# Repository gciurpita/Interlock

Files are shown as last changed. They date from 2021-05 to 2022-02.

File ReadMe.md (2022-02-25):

### RR Interlock - Bill Lupoli's New Haven



Arduino interlock route controller,
aligns multiple turnouts through interlock
by pressing buttons at either end of route.

Controller uses hardware shown at right.
~12V input top left to ~6V down converter to Arduino UNO board bottom left.
Three custom Tortoise Driver and I/O PCBs
using MCP23017 I2C I/O expander
to control up to 8 tortoise switch machines using LM324 op-amps and
eight GPIOs.

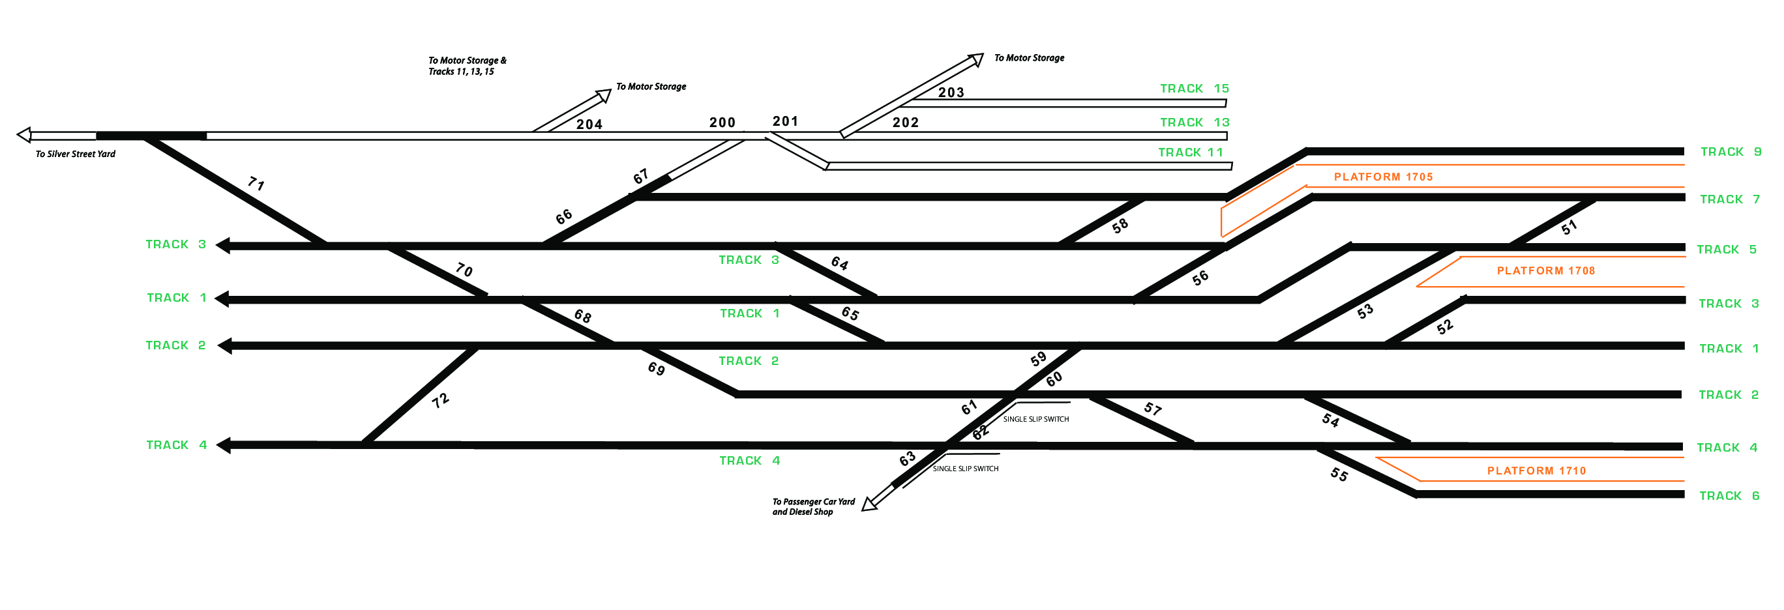
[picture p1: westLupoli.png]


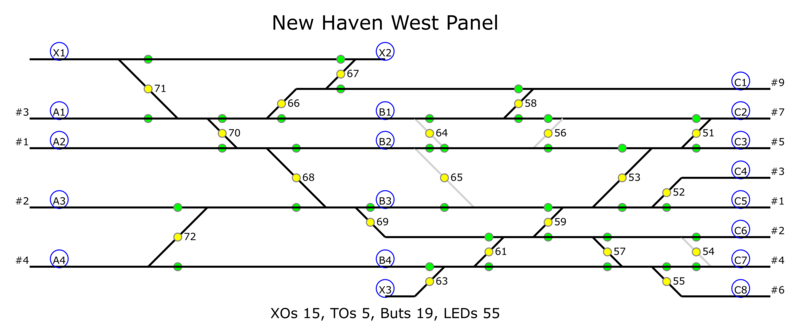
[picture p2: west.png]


<!-- -----------------------------------------------  ---------------------- -->
<h4> PCB Wire Connections </h4>

<table border=1 cellspacing=0 align=right>
 <tr> <th colspan=2> PCB 4
 <tr> <th> Sw <th> But
 <tr> <td align=center> &nbsp; <td align=center>  &nbsp;
 <tr> <td align=center> &nbsp; <td align=center>  &nbsp;
 <tr> <td align=center> &nbsp; <td align=center>  &nbsp;
 <tr> <td align=center> &nbsp; <td align=center>  &nbsp;

 <tr> <td align=center> &nbsp; <td align=center>  &nbsp;
 <tr> <td align=center> &nbsp; <td align=center>  &nbsp;
 <tr> <td align=center> &nbsp; <td align=center>  &nbsp;
 <tr> <td align=center> &nbsp; <td align=center>  &nbsp;
</table>

<table border=1 cellspacing=0 align=right>
 <tr> <th colspan=2> PCB 3
 <tr> <th> Sw <th> But
 <tr> <td align=center>  69 <td align=center>  A1
 <tr> <td align=center>  70 <td align=center>  A2
 <tr> <td align=center>  71 <td align=center>  A3
 <tr> <td align=center>  72 <td align=center>  A4
 <tr> <td align=center> &nbsp; <td align=center> B1
 <tr> <td align=center> &nbsp; <td align=center> B2
 <tr> <td align=center> &nbsp; <td align=center> B3
 <tr> <td align=center> &nbsp; <td align=center> B4
</table>

<table border=1 cellspacing=0 align=right>
 <tr> <th colspan=2> PCB 2
 <tr> <th> Sw <th> But
 <tr> <td align=center>  59 <td align=center>  C1
 <tr> <td align=center>  61 <td align=center>  C2
 <tr> <td align=center>  63 <td align=center>  C3
 <tr> <td align=center>  64 <td align=center>  C4
 <tr> <td align=center>  65 <td align=center>  C5
 <tr> <td align=center>  66 <td align=center>  C6
 <tr> <td align=center>  67 <td align=center>  C7
 <tr> <td align=center>  68 <td align=center>  C8
</table>

<table border=1 cellspacing=0 align=right>
 <tr> <th colspan=2> PCB 1
 <tr> <th> Sw <th> But
 <tr> <td align=center>  51 <td align=center>  X1
 <tr> <td align=center>  52 <td align=center>  X2
 <tr> <td align=center>  53 <td align=center>  X3
 <tr> <td align=center>  54 <td align=center>  &nbsp;

 <tr> <td align=center>  55 <td align=center>  &nbsp;
 <tr> <td align=center>  56 <td align=center>  &nbsp;
 <tr> <td align=center>  57 <td align=center>  &nbsp;
 <tr> <td align=center>  58 <td align=center>  &nbsp;
</table>

<a href=https://i.imgur.com/RJTQaR7.jpg target="_blank">
</a>

<!-- -----------------------------------------------  ---------------------- -->
<h4> Panel Description  </h4>

<i>westIntLck.cpp</i> contains tables describing the panel:
buttons, turnouts and routes.
This description requires a minimal understanding of programming
to make modifications.

<p>
Descriptions of both buttons and turnouts
includes identifying the corresponding
chip and port bit along with a label.

<p>
Buttons are described in <i>butIos []</i>.
<i>Ba1</i> is a numeric symbol uniquely identifying each button,
the <i>B</i> prefix identifies it as a button and
<i>a1</i> corresponds to the label on the panel.
The <i>0, 0, "A1"</i> identifies the input on
chip 0, port bit 0 (the first or least significant bit) and
a text string label, <i>A1</i>.
There are at most 8 bits on each chip,
some spare bits are available.

<blockquote><pre>
const PROGMEM ButIo_t butIos [] = {
    { Ba1, { 0, 0, "A1" }},
    ...
    { Bc6, { 1, 5, "C6" }},
    ...
    { Bc9, { 2, 0, "C9" }},
    { Bx1, { 2, 1, "X1" }},
    { Bx2, { 2, 2, "X2" }},
    ...
    { B_0, { 0, 0, ""   }},
};
</blockquote></pre>

There is an entry for each switch machine position.
<i>s02r</i> is the variable name of the entry used in the <i>routes</i> table.
The first three fields, <i>2, R, 1</i>,
include a numeric value for the switch machine,
a symbol, <i>N/R</i> identifying the position as normal/reverse and
the bit value, 0/1 for that position.
The last three fields,
<i>0, 1, "s02r"</i>, like the button entry
specify the chip, port bit and label.

<blockquote><pre>
// machine address and polarity
const PROGMEM SwMach_t s02n = {  2, N, 0, { 0, 1, "s02n" }};
const PROGMEM SwMach_t s02r = {  2, R, 1, { 0, 1, "s02r" }};

const PROGMEM SwMach_t s14n = { 14, N, 0, { 1, 5, "s14n" }};
const PROGMEM SwMach_t s14r = { 14, R, 1, { 1, 5, "s14r" }};

const PROGMEM SwMach_t s21n = { 21, N, 0, { 2, 4, "s21n" }};
const PROGMEM SwMach_t s21r = { 21, R, 1, { 2, 4, "s21r" }};
</blockquote></pre>

Routes are described in the routes table, <i>routes []</i>.
Each entry specifies a pair a buttons and
one or more switch machine position references (i.e. pointers).

<blockquote><pre>
const PROGMEM Route_t routes [] = {
    { Ba1, Bc1, { &s21r, &s19n, &s15r, &s14n, &s06n }},
    { Ba1, Bc2, { &s21r, &s19n, &s15n, &s10n, &s06n }},
    ...
    { Ba4, Bc4, { &s20n, &s16n, &s17n, &s11n, &s12n, &s07n, &s02r, &s01n }},
    ...
}
</blockquote></pre>

Some routes are ambiguous,
a pair of buttons can select more than one route.
<blockquote><pre>
    { Ba4, Bc3, { &s20n, &s16n, &s17n, &s11n, &s12n, &s07n, &s02r, &s01r }},
    { Ba4, Bc3, { &s20r, &s16n, &s17n, &s11n, &s12n, &s07n, &s02r, &s01r }},
</blockquote>

The code repeatedly
* monitors the button input ports
* detects that two or more buttons have been pressed
* uses <i>butIos []</i> to match the chip and port bit to button IDs
* searches the routes table for an entry with that pair of buttons, and
* sets the corresponding bits to position the switch
for each machine in the route.

<!-- -----------------------------------------------  ---------------------- -->
<hr>
<h4> Code Description </h4>

<b>setup ()</b> 
sets the serial monitor bit rate,
configures pins 5-13 as outputs,
initializes the I2C interface (i.e. <i>Wire</i>) and
calls <i>i2cCfg ()</i> to configure the
I/O expanders on each switch machine driver board.

<p>
<b>loop ()</b> invokes
<ul>
 <li> <i>ledStrobe ()</i>
 <li> <i>butScan ()</i>
 <li> <i>pcRead ()</i>
 <li> <i>tglTest ()</i>
</ul>

<p>
<b>ledStrobe (void)</b>
flashes/winks an LED at one of three different sequences,
on/off periods.

<p>
<b>butScan (void)</b>
reads GPIO-B, the button input port of each chip,
checks for a change in state,
waits WAIT_CNT iterations to debounce
before recognizing that one or more buttons have been pressed and 
calling <i>mapButtons ()</i> 

<p>
<b>mapButtons ()</b>
translates the chip and port bit of the button
into a button ID (e.g. <i>Ba1</i>) using <i>butFind ()</i>,
appending the button ID to <i>list []</i> 
<i>chkRoutes ()</i> is invoked
if two or more buttons are pressed.
<i>tglTestEn</i> is toggled
if the three: <i>Ba1, Ba3</i> and <i>Ba0</i> are pressed.

<p>
<b>butFind ()</b>
searches <i>butIos []</i> for
entries matching the chip and port bit arguments.
The following <i>butIos []</i> entry
specifies a button-ID, chip, port-bit and label
<blockquote>
    { Ba1, { 0, 0, "A1" }},
</blockquote>

<p>
<b>int chkRoutes ()</b> 
searches for a route entry with matching buttons.
The following <i>routes []</i> entry
specifies two buttons followed by one or more 
pointers (e.g. <i>&amp;s21n</i> to <i>SwMach_t</i>)
<blockquote>
    { Ba1, Bc1, { &s21r, &s19n, &s15r, &s14n, &s06n }},
</blockquote>
<i>chkButtons ()</i> is used to compare the button entries from a route
to the buttons in <i>list []</i> from <i>mapButtons ()</i>.

<p>
A <i>SwMach_t</i> entry specifies
a switch machine ID, position (i.e. N/R),
bit value for that position and <i>I2cBitDef_t</i> 
which specified a chip, port bit and label
<blockquote>
const PROGMEM SwMach_t s21r = { 21, R, 1, { 2, 4, "s21r" }};
</blockquote>

<p>
<b>int chkButtons ()</b>
compares each of three possible button arguments
to each entry in <i>list []</i>.

<p>
<b>void bitUpdate ()</b> 
updates a specific port bit on a specified chip
by reading and masking the port value 
to only update the state (0, 1) of the specified bit.

<p>
<b>i2cCfg () </b> 
configures GPIO-A and B direction registers
for output and input respectively.
It enables the pull-up resistors on GPIO-B.
set GPIO-B

<p>
<b>i2cWrite (int chip, int port, byte val) </b> 
writes the 8-bit value to the specific chip and port.
After writing the direction registers
it attempts to read them back and
discontinue the loop assuming not chip exists at that bus address.

<p>
<b>i2cWrite (int chip, int port, byte val) </b> 
writes the 8-bit value to the specific chip and port.

<p>
<b>test ()</b>
sequentially sets each port bit for 500 msec
first for GPIO-A and then GPIO-B (should have no effect).

<p>
<b>tglTest (void)</b>,
when enabled,
toggles all 8-its of GPIO-A on each chip every 4 seconds.
It first tests if <i>tglTestEn</i> is set.
It then tests if the time has expired.
It then inverts <i>tglTestState</i> and
writes it to GPIO-A of each chip.

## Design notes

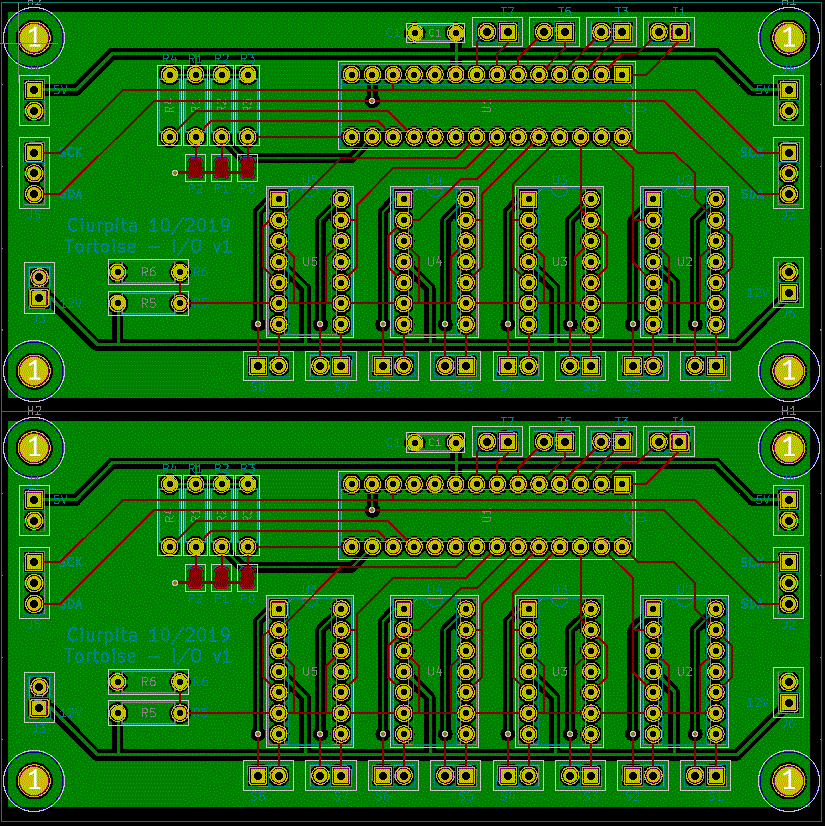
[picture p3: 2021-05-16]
SwMachDrvr/swMachDrvr.GIF

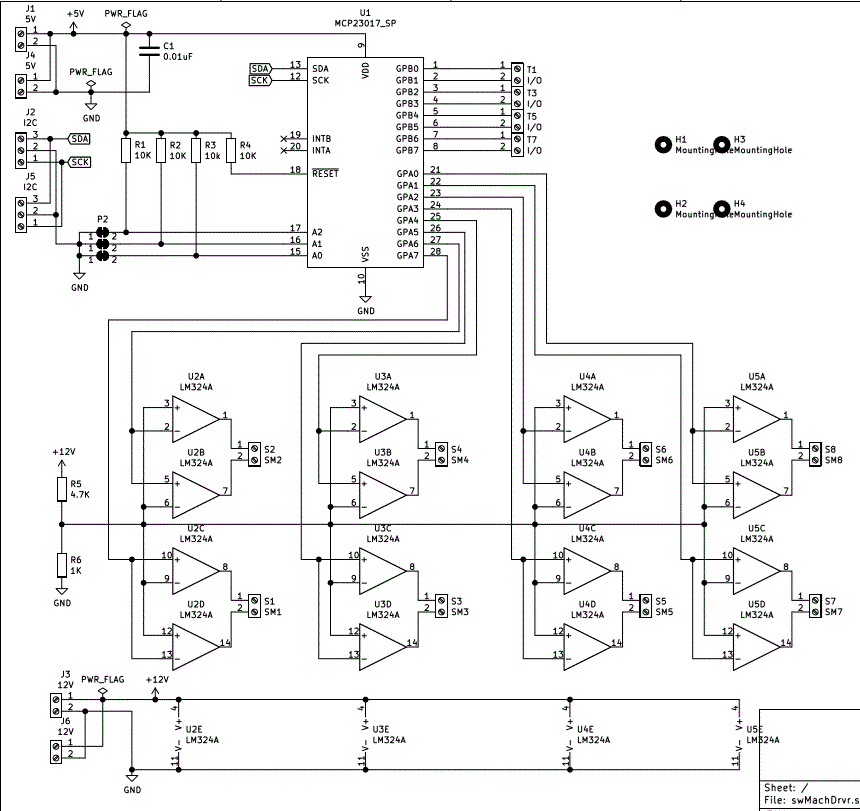
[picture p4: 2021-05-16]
SwMachDrvr/schem.GIF

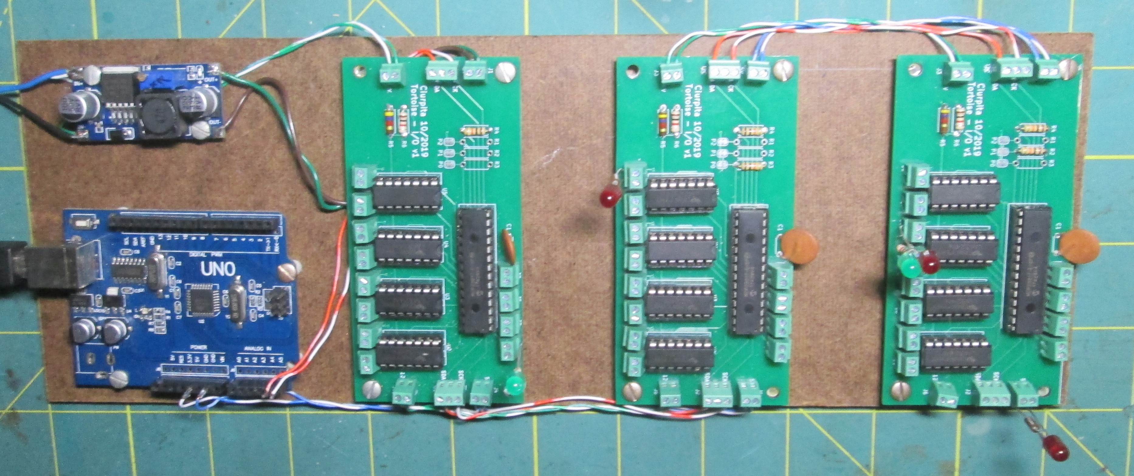
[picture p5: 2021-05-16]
SwMachDrvr/IMG_1342a.jpg

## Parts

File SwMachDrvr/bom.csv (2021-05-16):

Id | Designator | Package | Quantity | Designation | Supplier and ref
1 | J6,J3 | PinHeader_1x02_P2.54mm_Vertical | 2 | 12V
2 | S1 | PinHeader_1x02_P2.54mm_Vertical | 1 | SM1
3 | J4,J1 | PinHeader_1x02_P2.54mm_Vertical | 2 | 5V
4 | J5,J2 | PinHeader_1x03_P2.54mm_Vertical | 2 | I2C
5 | P2,P1,P0 | SolderJumper-2_P1.3mm_Bridged_RoundedPad1.0x1.5mm | 3 | br
6 | C1 | C_Disc_D4.3mm_W1.9mm_P5.00mm | 1 | 0.01uF
7 | H1,H2,H3,H4 | MountingHole_3.5mm | 4 | MountingHole
8 | R1,R2,R4 | R_Axial_DIN0207_L6.3mm_D2.5mm_P7.62mm_Horizontal | 3 | 10K
9 | R3 | R_Axial_DIN0207_L6.3mm_D2.5mm_P7.62mm_Horizontal | 1 | 10k
10 | R5 | R_Axial_DIN0207_L6.3mm_D2.5mm_P7.62mm_Horizontal | 1 | 4.7K
11 | R6 | R_Axial_DIN0207_L6.3mm_D2.5mm_P7.62mm_Horizontal | 1 | 1K
12 | U1 | DIP-28_W7.62mm_Socket | 1 | MCP23017_SP
13 | U2,U3,U4,U5 | DIP-14_W7.62mm_Socket | 4 | LM324A
14 | T1,T3,T5,T7 | PinHeader_1x02_P2.54mm_Vertical | 4 | I/O
15 | S2 | PinHeader_1x02_P2.54mm_Vertical | 1 | SM2
16 | S3 | PinHeader_1x02_P2.54mm_Vertical | 1 | SM3
17 | S4 | PinHeader_1x02_P2.54mm_Vertical | 1 | SM4
18 | S5 | PinHeader_1x02_P2.54mm_Vertical | 1 | SM5
19 | S6 | PinHeader_1x02_P2.54mm_Vertical | 1 | SM6
20 | S7 | PinHeader_1x02_P2.54mm_Vertical | 1 | SM7
21 | S8 | PinHeader_1x02_P2.54mm_Vertical | 1 | SM8

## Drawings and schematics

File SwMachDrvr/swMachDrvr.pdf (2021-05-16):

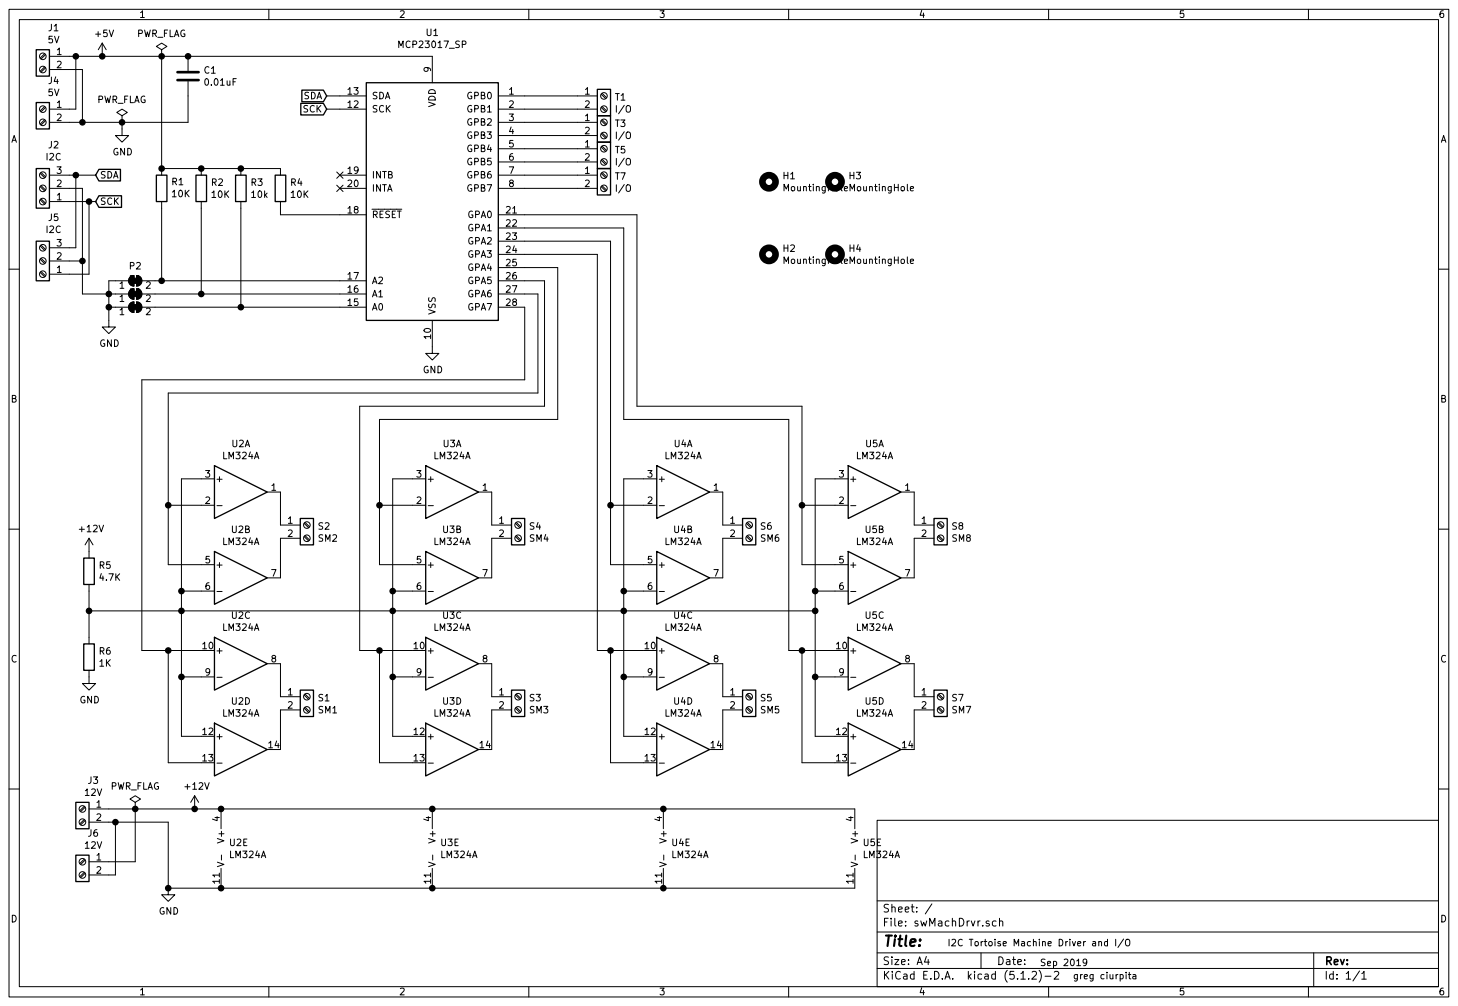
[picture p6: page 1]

I2C Tortoise Machine Driver and I/O

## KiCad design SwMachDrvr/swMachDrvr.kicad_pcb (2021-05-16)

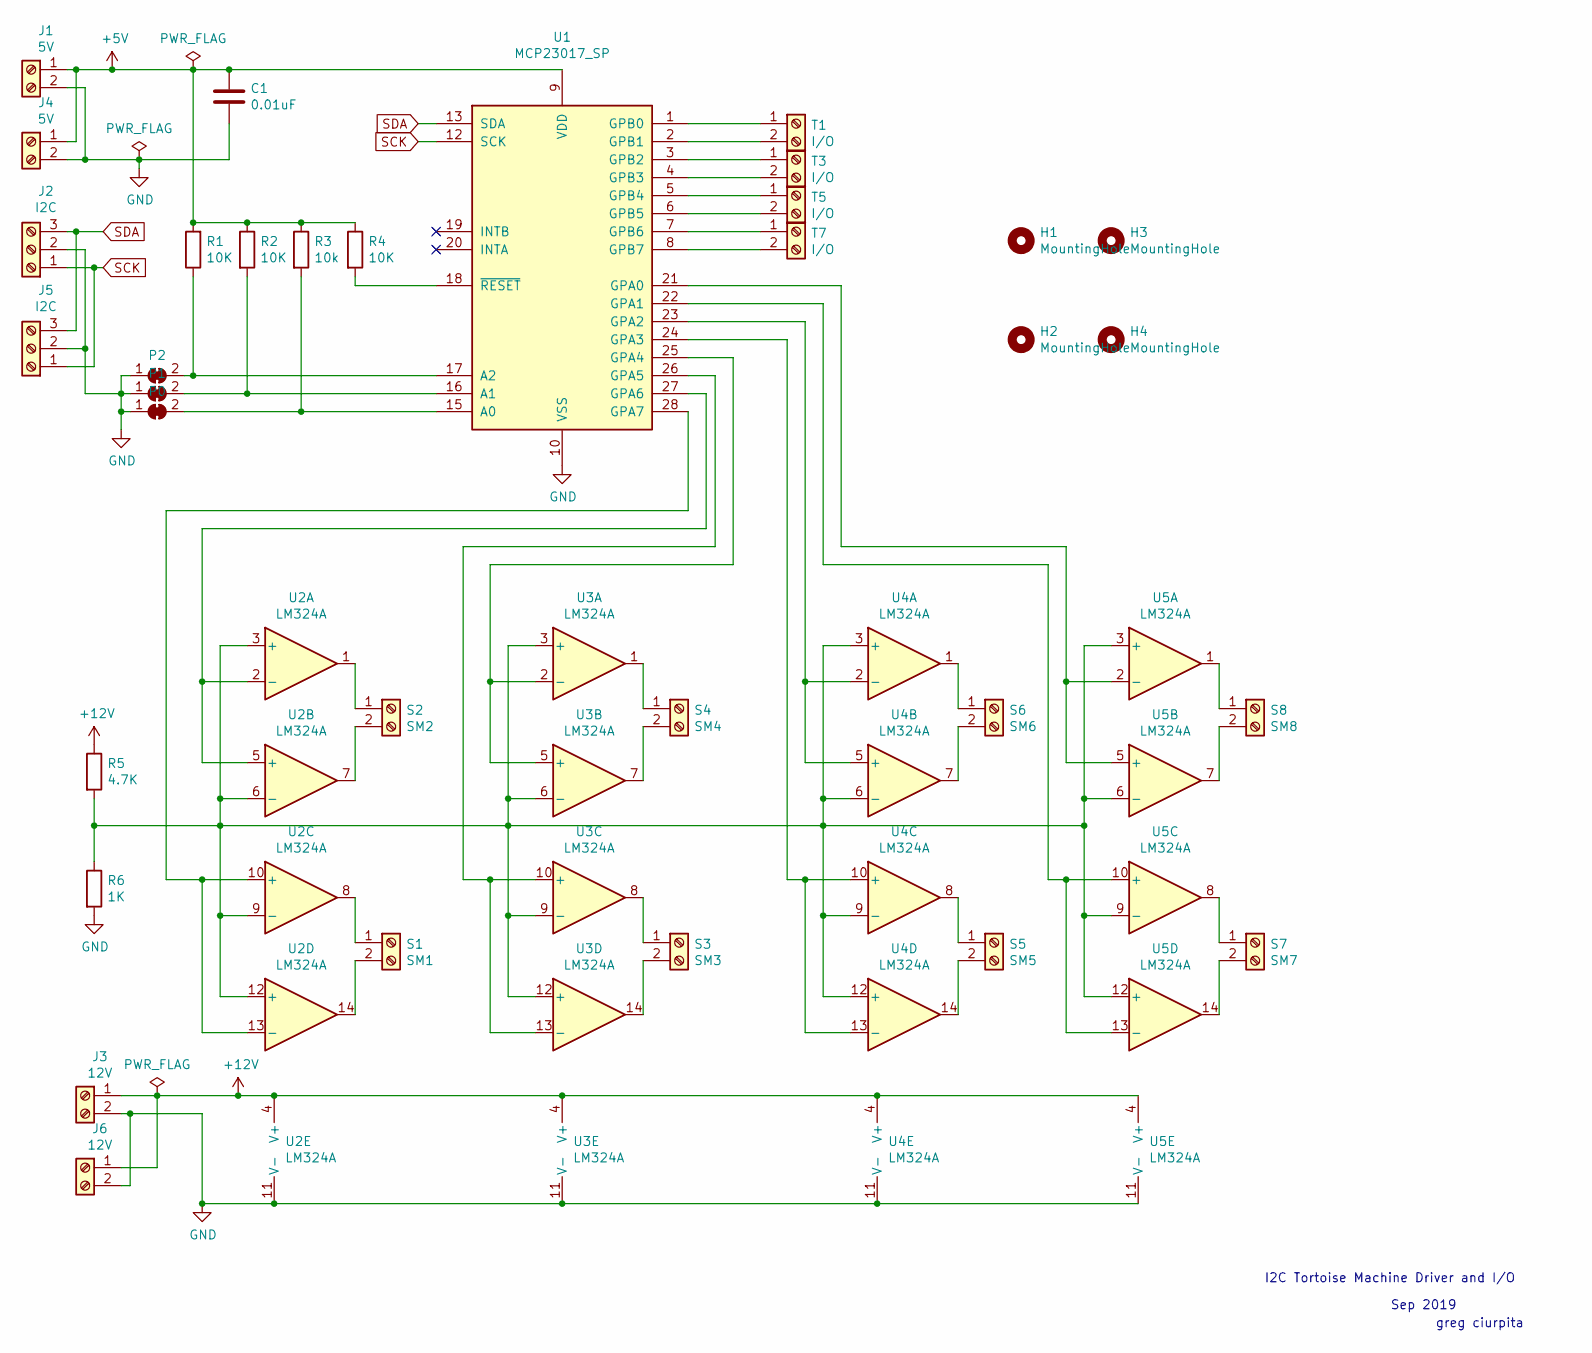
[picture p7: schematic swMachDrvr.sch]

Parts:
C1: 0.01uF; C_Disc_D4.3mm_W1.9mm_P5.00mm
H1, H2, H3, H4: MountingHole; MountingHole_3.5mm
J1, J4: 5V; PinHeader_1x02_P2.54mm_Vertical
J2, J5: I2C; PinHeader_1x03_P2.54mm_Vertical
J3, J6: 12V; PinHeader_1x02_P2.54mm_Vertical
P0, P1, P2: br; SolderJumper-2_P1.3mm_Bridged_RoundedPad1.0x1.5mm
R1, R2, R4: 10K; R_Axial_DIN0207_L6.3mm_D2.5mm_P7.62mm_Horizontal
R3: 10k; R_Axial_DIN0207_L6.3mm_D2.5mm_P7.62mm_Horizontal
R5: 4.7K; R_Axial_DIN0207_L6.3mm_D2.5mm_P7.62mm_Horizontal
R6: 1K; R_Axial_DIN0207_L6.3mm_D2.5mm_P7.62mm_Horizontal
S1: SM1; PinHeader_1x02_P2.54mm_Vertical
S2: SM2; PinHeader_1x02_P2.54mm_Vertical
S3: SM3; PinHeader_1x02_P2.54mm_Vertical
S4: SM4; PinHeader_1x02_P2.54mm_Vertical
S5: SM5; PinHeader_1x02_P2.54mm_Vertical
S6: SM6; PinHeader_1x02_P2.54mm_Vertical
S7: SM7; PinHeader_1x02_P2.54mm_Vertical
S8: SM8; PinHeader_1x02_P2.54mm_Vertical
T1, T3, T5, T7: I/O; PinHeader_1x02_P2.54mm_Vertical
U1: MCP23017_SP; DIP-28_W7.62mm_Socket
U2, U3, U4, U5: LM324A; DIP-14_W7.62mm_Socket

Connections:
+5V: C1.1, J1.1, J4.1, R1.2, R2.1, R3.1, R4.1, U1.9 (VDD)
+12V: J3.1, J6.1, R5.1, U2.4 (V+), U3.4 (V+), U4.4 (V+), U5.4 (V+)
GND: C1.2, J1.2, J2.2, J3.2, J4.2, J5.2, J6.2, P0.1 (A), P1.1 (A), P2.1 (A), R6.2, U1.10 (VSS), U2.11 (V-), U3.11 (V-), U4.11 (V-), U5.11 (V-)
unnamed: P0.2 (B), R3.2, U1.15 (A0)
unnamed: P1.2 (B), R2.2, U1.16 (A1)
unnamed: P2.2 (B), R1.1, U1.17 (A2)
unnamed: R4.2, U1.18 (~RESET~)
unnamed: R5.2, R6.1, U2.3 (+), U2.6 (-), U2.9 (-), U2.12 (+), U3.3 (+), U3.6 (-), U3.9 (-), U3.12 (+), U4.3 (+), U4.6 (-), U4.9 (-), U4.12 (+), U5.3 (+), U5.6 (-), U5.9 (-), U5.12 (+)
unnamed: S1.1, U2.8
unnamed: S1.2, U2.14
unnamed: S2.1, U2.1
unnamed: S2.2, U2.7
unnamed: S3.1, U3.8
unnamed: S3.2, U3.14
unnamed: S4.1, U3.1
unnamed: S4.2, U3.7
unnamed: S5.1, U4.8
unnamed: S5.2, U4.14
unnamed: S6.1, U4.1
unnamed: S6.2, U4.7
unnamed: S7.1, U5.8
unnamed: S7.2, U5.14
unnamed: S8.1, U5.1
unnamed: S8.2, U5.7
unnamed: T1.1, U1.1 (GPB0)
unnamed: T1.2, U1.2 (GPB1)
unnamed: T3.1, U1.3 (GPB2)
unnamed: T3.2, U1.4 (GPB3)
unnamed: T5.1, U1.5 (GPB4)
unnamed: T5.2, U1.6 (GPB5)
unnamed: T7.1, U1.7 (GPB6)
unnamed: T7.2, U1.8 (GPB7)
unnamed: U1.21 (GPA0), U5.2 (-), U5.5 (+)
unnamed: U1.22 (GPA1), U5.10 (+), U5.13 (-)
unnamed: U1.23 (GPA2), U4.2 (-), U4.5 (+)
unnamed: U1.24 (GPA3), U4.10 (+), U4.13 (-)
unnamed: U1.25 (GPA4), U3.2 (-), U3.5 (+)
unnamed: U1.26 (GPA5), U3.10 (+), U3.13 (-)
unnamed: U1.27 (GPA6), U2.2 (-), U2.5 (+)
unnamed: U1.28 (GPA7), U2.10 (+), U2.13 (-)
SCK: J2.1, J5.1, U1.12 (SCK)
SDA: J2.3, J5.3, U1.13 (SDA)

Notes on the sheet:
I2C Tortoise Machine Driver and I/O
Sep 2019
greg ciurpita

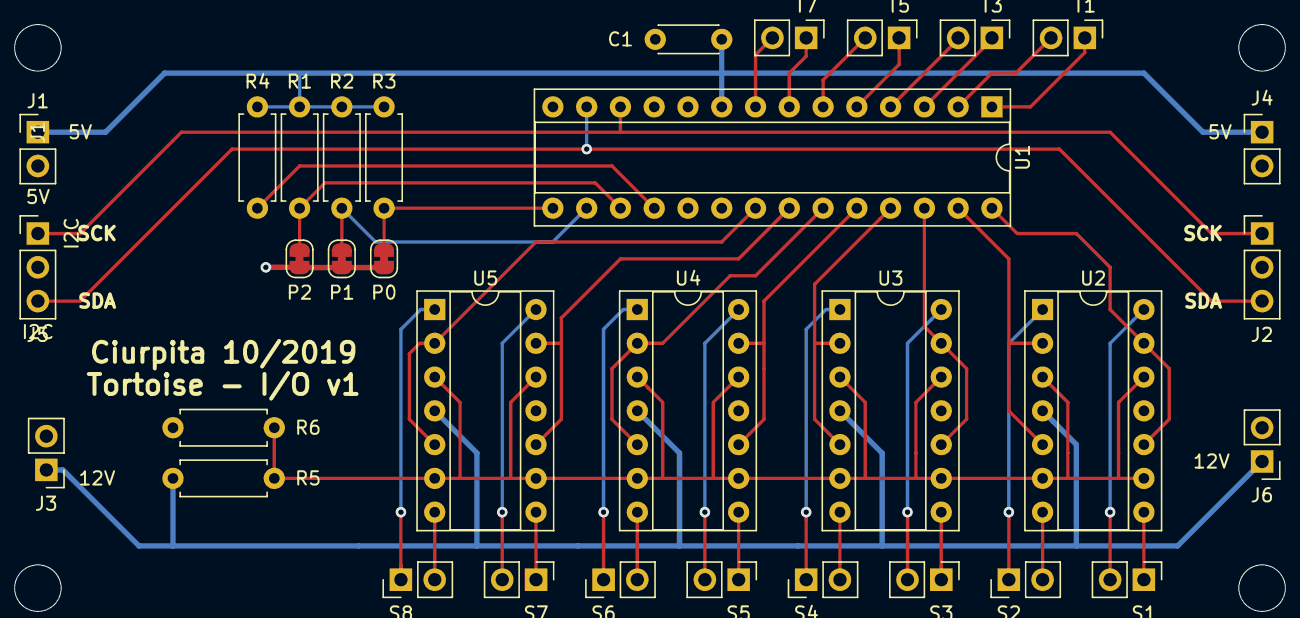
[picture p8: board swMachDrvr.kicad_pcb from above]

Board: 2 copper layers, 37 parts (0 on the bottom side), 42 nets.

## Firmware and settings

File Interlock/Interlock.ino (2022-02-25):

// New Haven West const interlock

const char version [] = "New Haven West 211012a";

#include <TimerOne.h>
#include "Wire.h"  // I2R operations

#include "westIntlck.h"
#include "mpc23017.h"

enum {
    Loop = 5,       // 5
    LedStr,         // 6
    PcRead,         // 7

    IoWr,           // 8
    IoRd,           // 9

    ButScan,        // 10
    TglTest,        // 11

    MapBut,         // 12
    ButFind,        // 13
    Route,          // 14
    ChkBut,         // 15
};


const int LED = 13;

int   dbg     = 1;
int   ledMode = 0;
char  s [100];

#define MAX_BUTS    3
But_t  list [MAX_BUTS];


#undef SIM
#ifdef SIM
byte pinXs   [] = { A1, A2, A3 };
#define N_XS    sizeof(pinXs)

byte  stateXs [N_XS];
But_t butXs   [N_XS] = { Bx1, Bx2, Bx3 };
#endif

// -----------------------------------------------------------------------------
//         Uno  Mega
//  SDA <- A4   20
//  SCL <- A5   21

#define MAX_CHIP    8

// I2C definitions

const int Chip20 = 0x20;
const int Chip21 = 0x21;
const int Chip22 = 0x22;
const int Chip23 = 0x23;
const int Chip24 = 0x24;
const int Chip25 = 0x25;

const int IoInp  = 0xFF;
const int IoOut  = 0x00;


byte chip    = Chip20;
byte port    = GPIOA;

// ---------------------------------------------------------
void i2cWrite (
    int     chip,
    int     port,
    byte    val )
{
    digitalWrite(IoWr, HIGH);

    chip += chip < Chip20 ? Chip20 : 0;

    if (2 < dbg)  {
        Serial.print   (F("  i2cWrite: chip "));
        Serial.print   (chip, HEX);
        Serial.print   (", port ");
        Serial.print   (port, HEX);
        Serial.print   (", val ");
        Serial.println (val, HEX);
    }

    Wire.beginTransmission (chip);
    Wire.write (port);    
    Wire.write (val);    
    Wire.endTransmission ();

    digitalWrite(IoWr, LOW);
}

// ---------------------------------------------------------
byte
i2cRead (
    int     chip,
    int     port )
{
    if (8 & dbg)
        return 0xFF;

    digitalWrite(IoRd, HIGH);

    chip += chip < Chip20 ? Chip20 : 0;

    Wire.beginTransmission (chip);
    Wire.write (port);    
    Wire.endTransmission ();

    Wire.requestFrom (chip, 1); //get 1 byte
    byte val =  Wire.read ();

    if (3 < dbg)  {
        Serial.print   (F("  i2cRead: chip "));
        Serial.print   (chip, HEX);
        Serial.print   (", port ");
        Serial.print   (port, HEX);
        Serial.print   (", val ");
        Serial.println (val, HEX);
    }

    digitalWrite(IoRd, LOW);
    return val;
}

// ---------------------------------------------------------
int nChip   = 0;

void i2cCfg (void)
{
    Serial.println (F("i2cCfg:"));
    for (nChip = 0; nChip < 8; nChip++)  {
        i2cWrite (nChip, IODIRA, IoOut);
        if (IoOut != i2cRead (nChip, IODIRA))
            break;

        i2cWrite (nChip, IODIRB, IoInp);
        if (IoInp != i2cRead (nChip, IODIRB))
            break;

        i2cWrite (nChip, GPPUB,  0xFF);

        Serial.print   ("i2cCfg: nChip ");
        Serial.println (nChip);
    }
}

// ---------------------------------------------------------
void i2cList (void)
{
    byte val0;
    byte val1;

    Serial.println (F("i2cList:"));

    for (int n = 0; n < nChip; n++)  {
        val0 = i2cRead (n, IODIRA);
        val1 = i2cRead (n, IODIRB);

        sprintf (s, " %s: 0x%02x 0x%02x", __func__, val0, val1);
        Serial.println (s);
    }
}

// ---------------------------------------------------------
// sequentially set each port bit
void
test (
    int     chip)
{
    Serial.print (F(" test: Gpio-A, chip 0x"));
    Serial.println (chip, HEX);

    for (byte bit = 0; bit < 8; bit++)  {
        i2cWrite (chip, GPIOA, 1 << bit);
        delay (500);
    }

    Serial.print (F(" test: Gpio-B, chip 0x"));
    Serial.println (chip, HEX);

    for (byte bit = 0; bit < 8; bit++)  {
        i2cWrite (chip, GPIOB, 1 << bit);
        delay (500);        // msec
    }
}

// ---------------------------------------------------------
int   tglTestCnt   = 0;
byte  tglTestEn    = 0;
byte  tglTestState = 0;
unsigned long  tglTestTime   = 0;
unsigned long  tglTestPeriod = 4000;

void
tglTest (void)
{
    if (! tglTestEn)
        return;

    unsigned long msec = millis();

    if ((msec - tglTestTime) < tglTestPeriod)
        return;

    digitalWrite(TglTest, HIGH);

    tglTestTime   = msec;
    tglTestState ^= 0xFF;

    for (int chip = 0; chip < nChip; chip++)
        i2cWrite (chip, GPIOA, tglTestState);

    Serial.print (F("tglTest: time "));
    Serial.print (tglTestTime);
    Serial.print (F(", cnt "));
    Serial.println (++tglTestCnt);

    digitalWrite(TglTest, LOW);
}

// ---------------------------------------------------------
void bitTgl (
    byte     chip,
    byte     reg,
    byte     bit )
{
    byte    val0  = i2cRead (chip, reg);
    byte    val1 = val0 ^ (1 << bit);

    if (dbg) {
        sprintf (s, " %s: chip %d, bit %d, val0 0x%02x, val1 0x%02x",
            __func__, chip, bit, val0, val1);
        Serial.println (s);
    }

    i2cWrite (chip, reg, val1);
}

// ---------------------------------------------------------
void bitUpdate (
    byte     chip,
    byte     reg,
    byte     bit,
    byte     bitVal )
{
    byte    val = i2cRead (chip, reg);
    
    val  &= ~(1 << bit);
    val  |= bitVal << bit;

    if (dbg) {
        sprintf (s, " %s: chip %d, bit %d, bitVal %d, val 0x%02x",
            __func__, chip, bit, bitVal, val );
        Serial.println (s);
    }

    i2cWrite (chip, reg, val);
}

// -----------------------------------------------------------------------------
int chkButtons (
    But_t*  list,
    byte    nButs,
    But_t   but0,
    But_t   but1,
    But_t   but2 )
{
    digitalWrite(ChkBut, HIGH);

    if (1 < dbg)  {
        sprintf (s, "  %s: [%d] %2d %2d %2d / %2d %2d %2d",
            __func__, nButs, list [0], list [1], list [2], but0, but1, but2);
        Serial.println (s);
    }

    int match = 0;
    for (byte n = 0; n < nButs; n++)  {
        match += but0 == list [n] ? 1 << n : 0;
        match += but1 == list [n] ? 1 << n : 0;
        match += but2 == list [n] ? 1 << n : 0;

        if (1 < dbg)  {
            Serial.print  (F("   chkButtons: n "));
            Serial.print  (n);
            Serial.print  (" list ");
            Serial.print  (list [n]);
            Serial.print  (" match ");
            Serial.println  (match);
        }
    }

    digitalWrite(ChkBut, LOW);

#if 0
    char s [40];
    sprintf (s, " %s: match %d, %d", __func__, match,
            B_0 != but2 ? 3 : (B_0 != but1 ? 2 : 1) );
    Serial.println (s);
#endif

    return (match == (B_0 != but2 ? 7 : (B_0 != but1 ? 3 : 1)));
}

// -----------------------------------------------------------------------------
SwMach_t *
loadSwMach (
    SwMach_t        *sm,
    const SwMach_t  *smPgm )
{
    sprintf (s, "%s:  sm %p, smPgm %p", __func__, sm, smPgm);
 // Serial.println (s);

    sm->id      = pgm_read_byte (& (smPgm->id));
    sm->pos     = pgm_read_byte (& (smPgm->pos));
    sm->bitVal  = pgm_read_byte (& (smPgm->bitVal));

    sm->io.chip = pgm_read_byte (& (smPgm->io.chip));
    sm->io.bit  = pgm_read_byte (& (smPgm->io.bit));


    return sm;
}

// -----------------------------------------------------------------------------
int chkRoutes (
    But_t*  list,
    byte    nButs )
{
    int  res = 0;

    sprintf (s, "%s: [%d] %d %d %d",
        __func__, nButs, list [0], list [1], list [2]);
    Serial.println (s);

    digitalWrite(Route, HIGH);

    for (const Route_t* r = routes;   ; r++)  {
        But_t _but0 = pgm_read_byte (& r->but0);
        But_t _but1 = pgm_read_byte (& r->but1);

        if (B_0 == _but0)
            break;

        if (! chkButtons (list, nButs, _but0, _but1, B_0))  {
#if 0
            char s [60];
            sprintf (s, " %s: %3d %3d no-match %3d %3d",
                __func__, list [0], list [1], _but0, _but1);
            Serial.println (s);
#endif
            continue;
        }

        SwMach_t* sm;
        for (int i = 0; (sm = pgm_read_word (& (r->list [i]))); i++)  {
            byte  _id    = pgm_read_byte (& (sm->id));
            byte  _pos   = pgm_read_byte (& (sm->pos));
            byte  _bitVal= pgm_read_byte (& (sm->bitVal));

            byte  _chip  = pgm_read_byte (& (sm->io.chip));
            byte  _bit   = pgm_read_byte (& (sm->io.bit));

            Serial.print   (F(" route   _id "));
            Serial.print   (_id);
            Serial.print   (F(", _pos "));
            Serial.print   (_pos);
            Serial.print   (F(", _bitVal "));
            Serial.print   (_bitVal);

            Serial.print   (F(" _chip "));
            Serial.print   (_chip);
            Serial.print   (F(", _bit "));
            Serial.println (_bit);

            if (B_N == _but1)
                bitTgl    (_chip, GPIOA, _bit);
            else
                bitUpdate (_chip, GPIOA, _bit, _bitVal);
        }

        res = 1;
        break;
    }

    digitalWrite(Route, LOW);
    return res;
}

// ---------------------------------------------------------
But_t
butFind (
    byte    chip,
    byte    bit )
{
    But_t   val = B_0;

    digitalWrite(ButFind, HIGH);

    if (dbg)  {
        Serial.print   (F("  butFind: chip "));
        Serial.print   (chip);
        Serial.print   (F(", bit "));
        Serial.println (bit);
    }

    for (const ButIo_t* b = butIos;    ; b++)  {
        byte _chip = pgm_read_byte (& b->io.chip);
        byte _bit  = pgm_read_byte (& b->io.bit);
        byte _but  = pgm_read_byte (& b->but);

        if (B_0 == _but)
            break;

        if (1 < dbg)  {
            Serial.print   (F("        "));
            Serial.print   (F(", _chip "));
            Serial.print   (_chip);
            Serial.print   (F(", _bit "));
            Serial.print   (_bit);
            Serial.print   (F(", _but "));
            Serial.println (_but);
        }

        if (chip == _chip && bit == _bit) {
            if (dbg)  {
                Serial.print   ("    found ");
                Serial.println (_but);
            }
            val = (But_t) _but;
            break;
        }
    }

    if (dbg)
        Serial.print ("\n");

    digitalWrite(ButFind, LOW);

    return val;
}

// ---------------------------------------------------------
// map bit changes to buttons
void
mapButtons (
    byte*   state,
    int     nState )
{
    byte   nButs           = 0;

    digitalWrite(MapBut, HIGH);

    for (byte  i = 0; i < nState; i++)  {
        if (1 < dbg)  {
            Serial.print  (F(" mapButtons: "));
            Serial.print  (i);
            Serial.print  (" ");
            Serial.println (state [i], HEX);
        }

        byte  val = state [i];

        for (int j = 0; j < 8; j++, val >>= 1)  {
            if (! (val & 1))  {
                list [nButs++] = butFind (i, j);

                if (MAX_BUTS == nButs)
                    goto done;
            }
        }
    }

    // process button presses
done:
    if (2 <= nButs)  {
        Serial.print (F("mapButtons:"));
        for (int j = 0; j < nButs; j++)  {
            Serial.print (" ");
            Serial.print (list [j]);
        }
        Serial.print ("\n");

        if (1 == chkRoutes (list, nButs))
            return;

        // check for test modes
        if (chkButtons (list, nButs, Ba1, Ba3, B_0))  {
            Serial.println (F("  test mode"));
            if (0 == tglTestEn)  {
                tglTestEn = 1;
                ledMode   = 1;
            }
            else {
                tglTestEn = 0;
                ledMode   = 0;
            }
        }
    }
    digitalWrite(MapBut, LOW);

}

// ---------------------------------------------------------
#define WAIT_CNT    10

void butScan (void)
{
    if (4 & dbg)
        return;

    static byte state [N_CHIP] = {};
    static byte cnt   [N_CHIP] = {};
    int    change   = 0;

 // if (tglTestEn) return;

    digitalWrite(ButScan, HIGH);

    // capture debounced inputs
    for (byte  i = 0; i < N_CHIP; i++)  {
        byte chip = Chip20 + i;
        byte val  = i2cRead (chip, GPIOB);

        if (state [i] == val)
            cnt [i] = 0;
        else  {
            if (0 == cnt [i])
                cnt [i] = WAIT_CNT;
            else if (0 == --cnt [i])  {
                state [i] = val;
                change++;

                if (1 < dbg)  {
                    Serial.print   (F(" butScan: chip "));
                    Serial.print   (chip, HEX);
                    Serial.print   (F("  "));
                    Serial.println (val, HEX);
                }
            }

            delay (1);      // msec
        }
    }

    // no further processing is no button input
    if (change)
        mapButtons (state, sizeof(state));

#ifdef SIM
    for (unsigned n = 0; n < N_XS; n++)  {
        byte but     = digitalRead (pinXs [n]);
        if (stateXs [n] != but)  {
            stateXs [n] = but;
            delay (10);

            if (LOW == but)  {
                if (Bx2 == butXs [n])  {
                    list [0] = Ba2;
                    list [1] = Bb2;
                }
                else {
                    list [0] = butXs [n];
                    list [1] = B_N;
                }

                chkRoutes (list, 2);
            }
        }
    }
#endif

    digitalWrite(ButScan, LOW);
}
// -----------------------------------------------------------------------------
// -----------------------------------------------------------------------------
void
listMachs (void)
{
    SwMach_t    sm;
    char        desc [20];

    sm.io.desc = desc;

    for (const SwMach_t **p = smListRev; 0 != *p; p++)  {
        loadSwMach (&sm, *p);

        sprintf (s, " %s: id %2d, pos %d, val %d, chip %d, bit %d",
            __func__, sm.id, sm.pos, sm.bitVal, sm.io.chip, sm.io.bit);
        Serial.println (s);
    }
}

// ---------------------------------------------------------
// process commands from serial monitor
void
swTurnout (
    int  id )
{
    SwMach_t    sm;

    for (const SwMach_t **p = smListRev; 0 != *p; p++)  {
        loadSwMach (&sm, *p);

        if (sm.id == id)  {
            sprintf (s, "%s: id %2d, pos %d, val %d, chip %d, bit %d",
                __func__, sm.id, sm.pos, sm.bitVal, sm.io.chip, sm.io.bit);
            Serial.println (s);


            bitTgl (sm.io.chip, GPIOA, sm.io.bit);
            return;
        }
    }

    sprintf (s, "%s: id %2d, not found", __func__, id);
    Serial.println (s);
}

// ---------------------------------------------------------
// process commands from serial monitor
void
pcRead (void)
{
    digitalWrite(PcRead, HIGH);

    static int  val  = 0;

#define None    -1
    static int  valA = None;
    static int  valB = None;

    if (Serial.available()) {
        int c = Serial.read ();

        switch (c)  {
        case '0':
        case '1':
        case '2':
        case '3':
        case '4':
        case '5':
        case '6':
        case '7':
        case '8':
        case '9':
            val = c - '0' + (10 * val);
            if (1 < dbg)
                Serial.println (val);
            break;

        case ' ':
            val = 0;
            break;

        case 'D':
            dbg = val;
            val = 0;
            break;

        case 'a':
            valA = Ba1 + val;
            val  = 0;
            break;

        case 'b':
            valB = Bb1 + val;
            val  = 0;
            break;

        case 'c':
            chip = val;
            val  = 0;
            break;

        case 'l':
            listMachs ();
            break;

        case 'p':
            port = val;
            val  = 0;
            break;

        case 'R':
            i2cCfg ();
            break;

        case 'r':
            Serial.print   ("read: chip ");
            Serial.print   (chip, HEX);
            Serial.print   (", port ");
            Serial.print   (port, HEX);
            Serial.print   (",  ");
            Serial.println (i2cRead (chip, port));
            break;

        case 'S':
            for (int port = 0; port <= 0x15; port++)  {
                Serial.print   (" read: chip ");
                Serial.print   (chip, HEX);
                Serial.print   (", port ");
                Serial.print   (port, HEX);
                Serial.print   (",  ");
                Serial.println (i2cRead (chip, port), HEX);
            }
            break;

        case 's':
            swTurnout (val);
            val = 0;
            break;

        case 'T':
            tglTestEn  ^= 1;
            ledMode = tglTestEn ? 1 : 0; 
            break;

        case 't':
            test (chip);
            break;

        case 'w':
            i2cWrite (chip, port, val);
            val  = 0;
            break;

        case 'V':
            Serial.print ("\nversion: ");
            Serial.println (version);
           break;

        case 'v':
            i2cList ();
            break;

        case '?':
            Serial.print (F("  # c  set chip 0-7 val\n"));
            Serial.print (F("    l  list machines\n"));
            Serial.print (F("  # p  set port (0-output/1-input) val\n"));
            Serial.print (F("    R  reconfig chips\n"));
            Serial.print (F("    r  read chip, port\n"));
            Serial.print (F("    S  read all registers of chip\n"));
            Serial.print (F("    s  switch turnout\n"));
            Serial.print (F("    T  en/disable tglTest\n"));
            Serial.print (F("    t  sequentially set each bit in GPIO-A/B\n"));
            Serial.print (F("  # w  write 8-bit val to chip/port\n"));
            Serial.print (F("    V  version\n"));
            Serial.print (F("    v  list chip registers\n"));
            break;

        case '\n':      // process simulated button input
            if (None != valA && None != valB)  {
                sprintf (s, "%s: Ba %2d, Bb %2d", __func__, valA, valB);
                Serial.println (s);

                list [0] = (But_t) valA;
                list [1] = (But_t) valB;
                chkRoutes (list, 2);

                valA = valB = None;
            }
            break;

        default:
            Serial.print ("unknown: ");
            Serial.println (c);
            break;
        }
    }
    digitalWrite(PcRead, LOW);
}

// -----------------------------------------------------------------------------
typedef struct {
    unsigned long   on;
    unsigned long   off;
} LedMode_t;

LedMode_t ledModes [] = {
    { 100, 900 },
    {  50, 200 },
    { 100, 150 },
};

unsigned long   msec = 0;
unsigned long   last = 0;

void
ledStrobe ()
{
    digitalWrite(LedStr, HIGH);
    msec = millis();
    if (HIGH == digitalRead (LED))  {
        if (ledModes [ledMode].on < (msec - last))  {
            digitalWrite(LED, LOW);
            last = msec;
        }
    }
    else  {
        if (ledModes [ledMode].off < (msec - last))  {
            digitalWrite(LED, HIGH);
            last = msec;
        }
    }
    digitalWrite(LedStr, LOW);
}

// -------------------------------------
void
loop ()
{
    digitalWrite(Loop, HIGH);
    ledStrobe ();

    butScan ();
    pcRead ();

    tglTest ();
    digitalWrite(Loop, LOW);
}

// -----------------------------------------------------------------------------
void setup()
{
    Serial.begin(9600);
    Serial.println (version);

    for (int pin = 5; pin <= 13; pin++)  {
        pinMode(pin, OUTPUT);
        digitalWrite(pin, HIGH);
    }

    Wire.begin();    //start I2C bus

    i2cCfg ();

#ifdef SIM
    Serial.println (" --------- SIM ---------");
    for (unsigned n = 0; n < N_XS; n++)  {
        pinMode (pinXs [n], INPUT_PULLUP);
        stateXs [n] = digitalRead (pinXs [n]);
    }
#endif
}

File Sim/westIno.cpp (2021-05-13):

// New Haven West const interlock

const char version [] = "New Haven West 191120a";

#include "Arduino.h"    // simulation

#include "Wire.h"  // I2R operations

#include "westIntlck.h"
#include "mpc23017.h"


const int LED = 13;

unsigned int dbg    = 1;
int ledMode         = 0;

// ---------------------------------------------------------
void prTxtVal (
    const char* text,
    int         val,
    int         fmt,
    bool        nl )
{
    Serial.print (text);
    Serial.print (val, fmt);
    if (nl)
        Serial.print ("\n");
}

// -----------------------------------------------------------------------------
//         Uno  Mega
//  SDA <- A4   20
//  SCL <- A5   21

#define MAX_CHIP    8

// I2C definitions

const int Chip20 = 0x20;
const int Chip21 = 0x21;
const int Chip22 = 0x22;
const int Chip23 = 0x23;
const int Chip24 = 0x24;
const int Chip25 = 0x25;

const int IoInp  = 0xFF;
const int IoOut  = 0x00;


byte chip    = Chip20;
byte port    = GPIOA;

// ---------------------------------------------------------
void i2cWrite (
    int     chip,
    int     port,
    byte    val )
{
    chip += chip < Chip20 ? Chip20 : 0;

    if (0 < dbg)  {
        prTxtVal   ("   i2cWrite: chip ", chip, HEX, 0);
        prTxtVal   (", port ",            port, HEX, 0);
        prTxtVal   (", val ",             val,  HEX, 1);
    }

    Wire.beginTransmission (chip);
    Wire.write (port);    
    Wire.write (val);    
    Wire.endTransmission ();
}

// ---------------------------------------------------------
byte
i2cRead (
    int     chip,
    int     port )
{
    if (8 & dbg)
        return 0xFF;

    chip += chip < Chip20 ? Chip20 : 0;

    Wire.beginTransmission (chip);
    Wire.write (port);    
    Wire.endTransmission ();

    Wire.requestFrom (chip, 1); //get 1 byte
    byte val =  Wire.read ();

    if (3 < dbg)  {
        prTxtVal   ("   i2cRead:  chip ", chip, HEX, 0);
        prTxtVal   (", port ",            port, HEX, 0);
        prTxtVal   (", val ",             val,  HEX, 1);
    }

    return val;
}

// ---------------------------------------------------------
int nChip   = 0;

void i2cCfg (void)
{
    Serial.println (" i2cCfg:");
    for (nChip = 0; nChip < 8; nChip++)  {
        i2cWrite (nChip, IODIRA, IoOut);
        if (IoOut != i2cRead (nChip, IODIRA))
            break;

        i2cWrite (nChip, IODIRB, IoInp);
        if (IoInp != i2cRead (nChip, IODIRB))
            break;

        i2cWrite (nChip, GPPUB,  0xFF);

        prTxtVal (" i2cCfg: nChip ", nChip, DEC, 1);
    }
}

// ---------------------------------------------------------
// toggle output bits every 4 sec 
int   tglTestCnt   = 0;
byte  tglTestEn    = 0;
byte  tglTestState = 0;
unsigned long  tglTestTime   = 0;
unsigned long  tglTestPeriod = 4000;

static void
tglTest (void)
{
    if (! tglTestEn)
        return;

    unsigned long msec = millis();

    if ((msec - tglTestTime) < tglTestPeriod)
        return;

    tglTestTime   = msec;
    tglTestState ^= 0xFF;

    for (int chip = 0; chip < nChip; chip++)
        i2cWrite (chip, GPIOA, tglTestState);

    prTxtVal ("tglTest: time ", tglTestTime, DEC, 0);
    prTxtVal (", cnt ", ++tglTestCnt,        DEC, 1);
}

// -----------------------------------------------------------------------------
void
routeAlign (
    int     routeIdx )
{
    static byte state [MAX_CHIP] =  {};

    const Route_t*  r = &routes [routeIdx];
    const SwMach_t* sm;

    prTxtVal (" routeAlign: route idx ", routeIdx, DEC, 1);

    for (int i = 0; (sm = pgm_read_word (& (r->list [i]))); i++)  {
        byte  _id    = pgm_read_byte (& (sm->id));
        byte  _pos   = pgm_read_byte (& (sm->pos));
        byte  _bitVal= pgm_read_byte (& (sm->bitVal));

        byte  _chip  = pgm_read_byte (& (sm->io.chip));
        byte  _bit   = pgm_read_byte (& (sm->io.bit));

        prTxtVal   ("  routeAlign: mach id ", _id, DEC, 0);
        prTxtVal   (", pos ",      _pos,    DEC, 0);
        prTxtVal   (", bitVal ",   _bitVal, DEC, 0);
        prTxtVal   (", _chip ",    _chip,   DEC, 0);
        prTxtVal   (", _bit ",     _bit,    DEC, 1);

        state [_chip] = _bitVal
                        ? state [_chip] |   1 << _bit
                        : state [_chip] & ~(1 << _bit);
    }

    for (byte chip = 0; chip < nChip; chip++)
        i2cWrite (chip, GPIOA, state [chip]);
}

// -----------------------------------------------------------------------------
// search for route matching buttons
// update bits in state []
// write state to chips

static int routeFind (
    But_t*  list,
    byte    nButs )
{
    int  res = 0;
    Serial.println (" routeFind: ");

    for (int i = 0;   ; i++)  {
        const Route_t* r = &routes [i];

        But_t _but0 = pgm_read_byte (& r->but0);
        But_t _but1 = pgm_read_byte (& r->but1);

        if (B_0 == _but0)
            break;

        if (   (_but0 == list [0] && _but1 == list [1])
            || (_but1 == list [0] && _but0 == list [1]) ) {
            routeAlign (i);
            break;
        }
    }

    return res;
}

// ---------------------------------------------------------
// search button table for matching chip/bit
static But_t
butFind (
    byte    chip,
    byte    bit )
{
    But_t   val = B_0;

    for (const ButIo_t* b = butIos;    ; b++)  {
        byte _chip = pgm_read_byte (& b->io.chip);
        byte _bit  = pgm_read_byte (& b->io.bit);
        byte _but  = pgm_read_byte (& b->but);

        if (B_0 == _but)
            break;

        if (chip == _chip && bit == _bit) {
            if (dbg)  {
                prTxtVal ("    butFind: chip ", chip, DEC, 0);
                prTxtVal (", bit ", bit, DEC, 0);
                prTxtVal (", but ", _but, DEC, 1);
            }
            val = (But_t) _but;
        }
    }

    if (val == B_0 && dbg)  {
        prTxtVal ("    butFind: chip ", chip, DEC, 0);
        prTxtVal (", bit ", bit, DEC, 0);
        prTxtVal (", unknown ", 0, DEC, 1);
    } 

    return val;
}
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

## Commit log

2021-05-16 KiCad files
    [bom.csv, swMachDrvr.kicad_pcb, swMachDrvr.sch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]
2021-07-10 corrected butScan case
2021-07-11 added wiring table
2021-07-16 updated diagram, combined turnouts & separate wiring tables
2021-07-16 removed suggest button D1 from diagram
2021-07-16 rewrote introduction describing board
2021-07-24 added button 'a' and 'b' cmds and break chkRoutes() when found
2021-08-10 reversed chips used by buttons
2021-08-10 added i2cList(), use F() to reduce ram, indent multiple msgs
2021-08-11 reordered button inputs
2021-08-11 button numbering
2021-08-23 narrows PCB sw/button table
2021-09-01 route correction - use sw#56
    [Interlock.ino]
2021-09-09 moved buttons to correct PCBs and added 4th PCB (spare)
2021-09-09 added one button Bx1 route
2021-09-09 added SIM cases to test one-button toggle
2021-10-12 switch 61 fixes
